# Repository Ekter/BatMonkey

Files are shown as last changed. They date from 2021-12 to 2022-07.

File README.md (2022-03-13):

# BatMonkey
This is the Bat Monkey, a monkey-like robot monitored by phone and controlled by arduino, whose purpose is to climb trees.

 [Gantt diagram]( https://online.officetimeline.com/shareable-link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)

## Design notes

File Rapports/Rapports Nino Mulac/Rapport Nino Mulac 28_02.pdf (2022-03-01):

# Bat Monkey

Rapport de la huitième séance(28 février) :
Pendant la séance, nous avons essayé le montage avec 8 moteurs. Nous ne l’avions jamais fait avant, et nous avons bien fait de vérifier que ça marche puisque la carte subit des pertes de tension le long de son circuit interne, qui empêchent plus de 4 moteurs d’être “attachés”(les moteurs se mettent ainsi à consommer du courant). Les 8 moteurs alimentés simultanément étaient parfois “ramollis” sans raison, et se laissaient tomber alors que le programme leur imposait un angle, ou se déplaçaient cran par cran quand on leur demandait un mouvement continu.
Nous avons désormais un “driver moteur” fait main par M. Masson équipé de câbles de cuivre de 1.5 mm qui conduisent beaucoup mieux l’électricité permettant ainsi d’éviter les chutes de tension.
Pendant la semaine, nous allons devoir tester les fonctions que nous avions écrites pour garder un mouvement linéaire par le calcul :
float getPhi(Servo servo, float i)
//i position de l'arbre par rapport au bras. ex: -1 indique 1 centimètre d'écart, 2 indique que le robot est enfoncé de 2 centimètres dans l'arbre
{
return acos(((i - 8.5 * cos(toAngle(servo.read()))) / 16));
}

float toAngle(float n)
{
return n * 3.14 / 180;
}

float toN(float a)
{
return a * 180 / 3.14;
}
Les fonctions toAngle et toN doivent être modifiées pour prendre en compte l’angle de chaque moteur, et tout devrait fonctionner ensuite.
Il ne nous restera qu’à découper les bras et y planter les clous.

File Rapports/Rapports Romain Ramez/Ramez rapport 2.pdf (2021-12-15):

## Ramez Romain

# BAT MONKEY SÉANCE N°2

J’ai commencé par finir la modalisation du Bat Monkey, en assemblant toutes les pièces entre elles, sur OneShape, et en modélisant un arbre pour mieux m’imager le principe de grimpe !

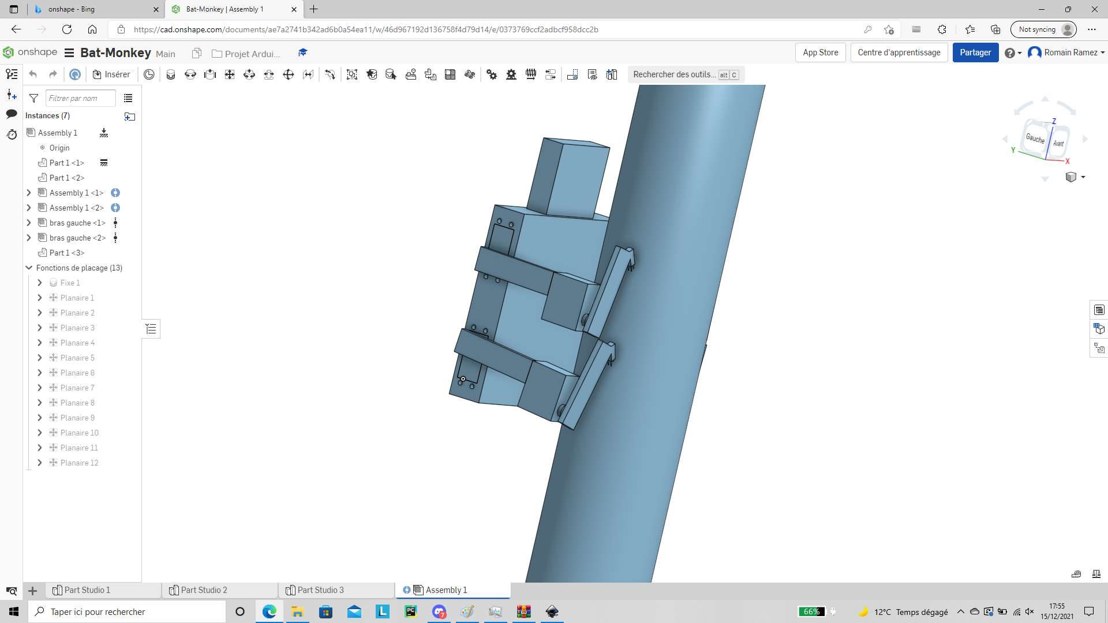
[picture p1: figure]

Ensuite, sous conseil du brillant professeur, nous avons décider de partir sur deux méthodes de grimpes différentes !
Je me suis donc mis à travailler sur une méthode où le Bat Monkey grimperai à l’arbre en s’accrochant (toujours à l’aide de piques) puis en se tractant à l’aide d’une crémaillère pour remonter au niveau des bras.

Modélisation du Bat Monkey

Modélisation des bras/ de la crémaillère
pour les premières tentative

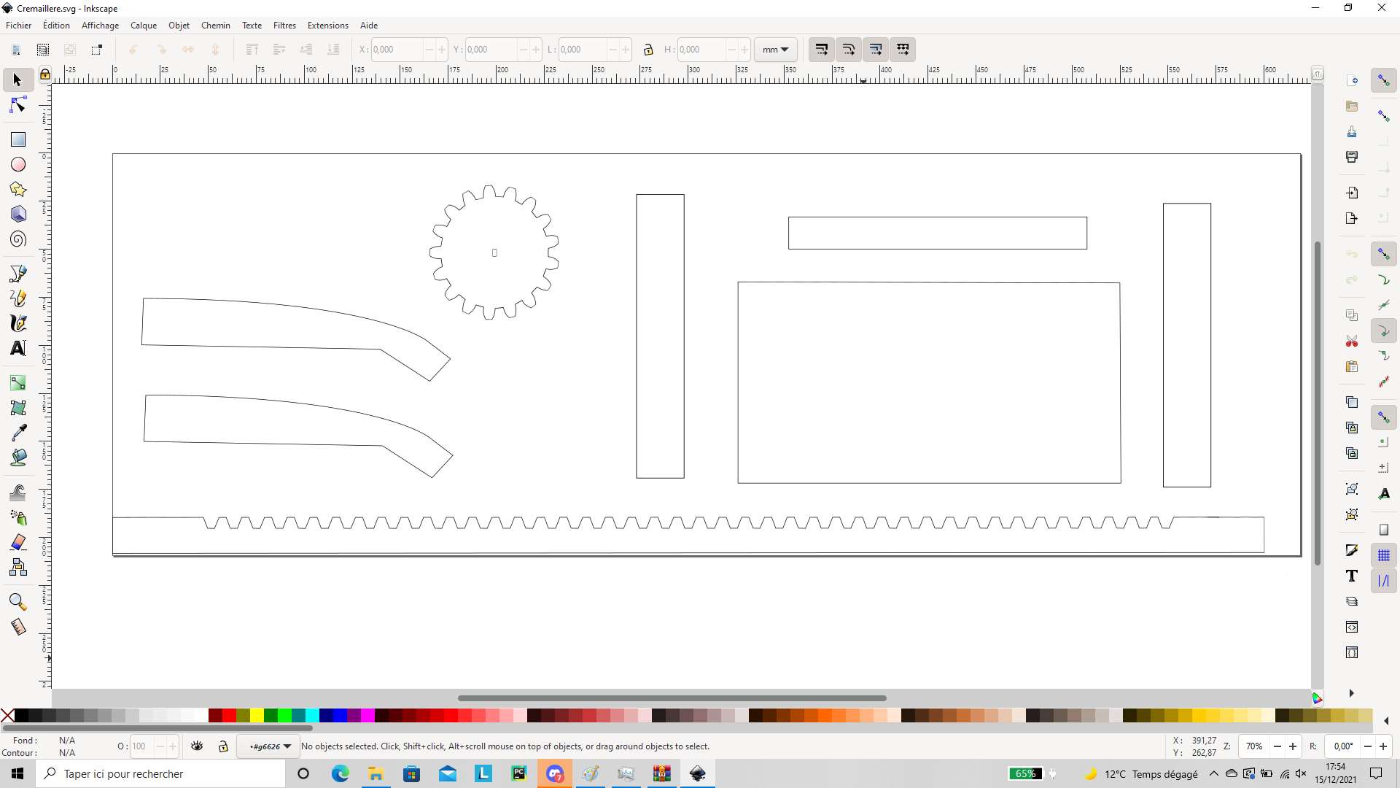
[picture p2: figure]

Enfin, j’ai pu aller faire découper tout cela à la coupeuse laser. Mais pour une raison que tout le monde ignore, le laser n’a pas transpercé le bois ( à 2 reprises… ), alors nous ne pouvons pas encore faire nos essais. Nous iront récupérer les morceaux de bois coupés vendredi au FabLab !

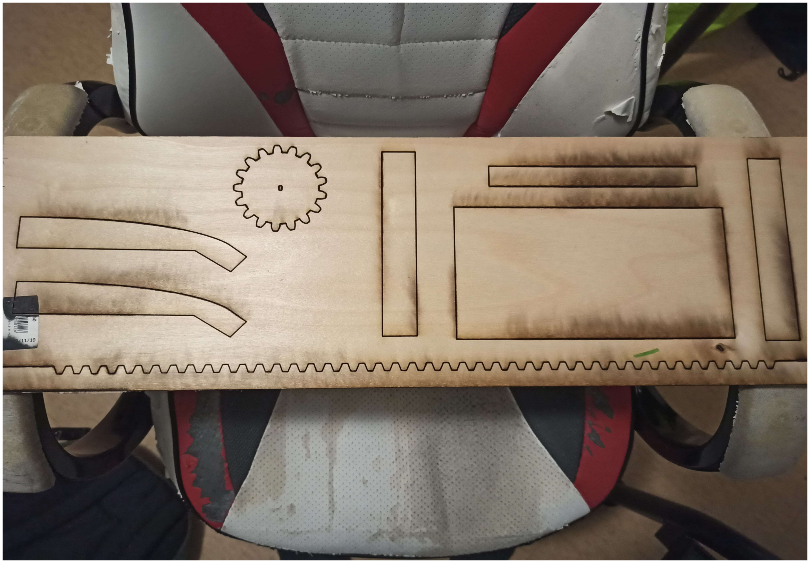
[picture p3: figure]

Planche de bois « presque » découpées

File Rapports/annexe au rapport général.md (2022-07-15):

# annexe

L'ensemble du programme est réécrit en algorithmes en language naturel [ici](https://github.com/Ekter/BatMonkey/tree/main/Code/algorithmes)

Vous pouvez aussi consulter le [code source](https://github.com/Ekter/BatMonkey/blob/main/Code/moteurs3/moteurs3.ino)

Ou voir la liste des composants et les shémas électroniques [ici](https://github.com/Ekter/BatMonkey/tree/main/Mod%C3%A8les/fritzing)

Au plaisir,

icon_BM

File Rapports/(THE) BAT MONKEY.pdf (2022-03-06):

# BAT MONKEY

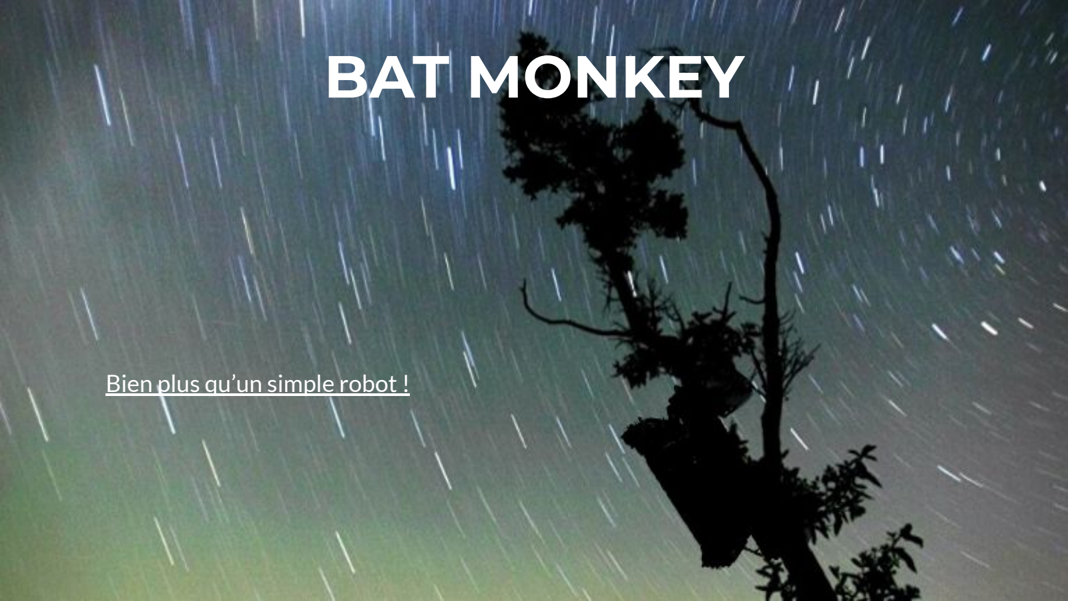
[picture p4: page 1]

### Bien plus qu’un simple robot !

# Sommaire

- L’idée
- Le plan
- Les échecs
- Les 1001 programmes
- Appli
- Son futur

# Pourquoi faire le Bat Monkey ?

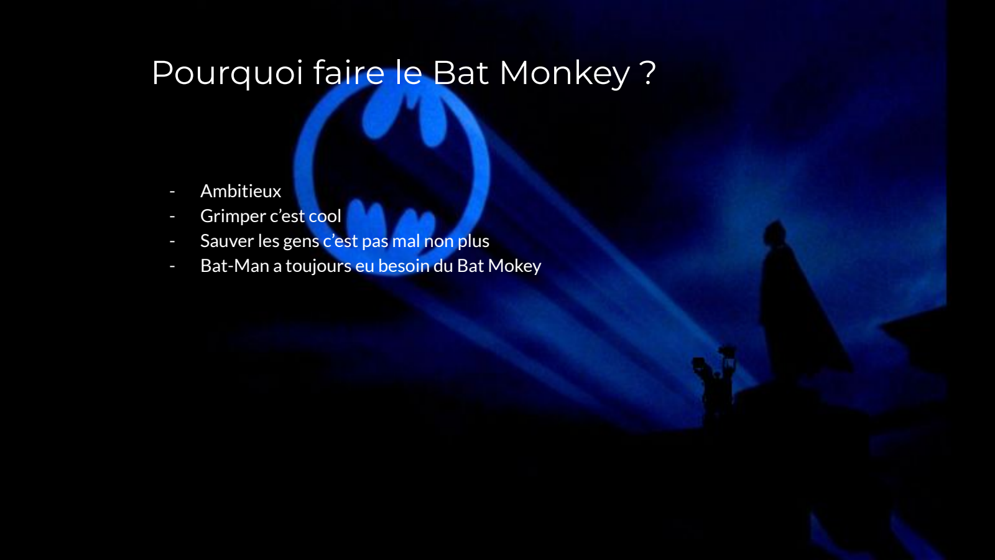
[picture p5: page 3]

- Ambitieux
- Grimper c’est cool
- Sauver les gens c’est pas mal non plus
- Bat-Man a toujours eu besoin du Bat Mokey

# Comment faire ?

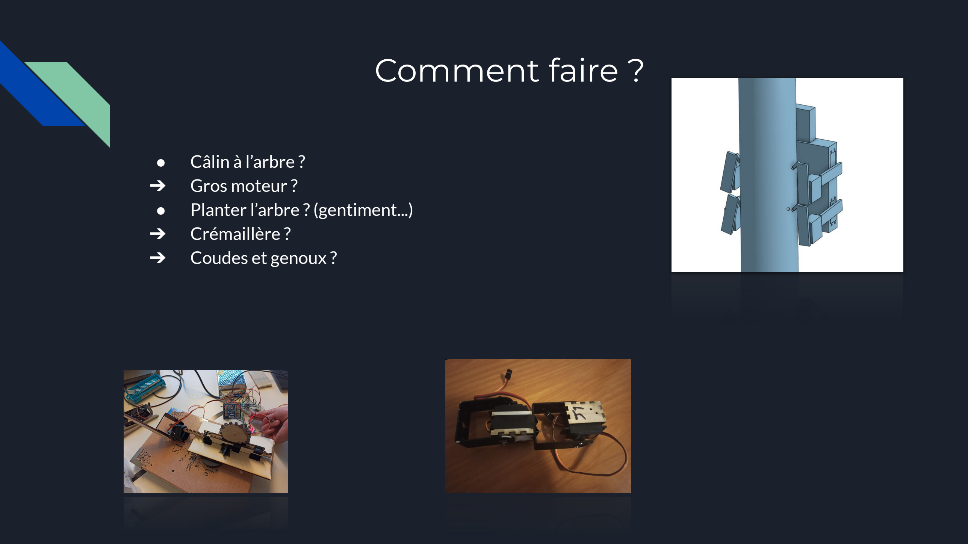
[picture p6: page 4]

- Câlin à l’arbre ?
➔ Gros moteur ?
- Planter l’arbre ? (gentiment...)
➔ | Crémaillère ?
➔ | Coudes et genoux ?

# Les ratés

# LA CREMAILLERE

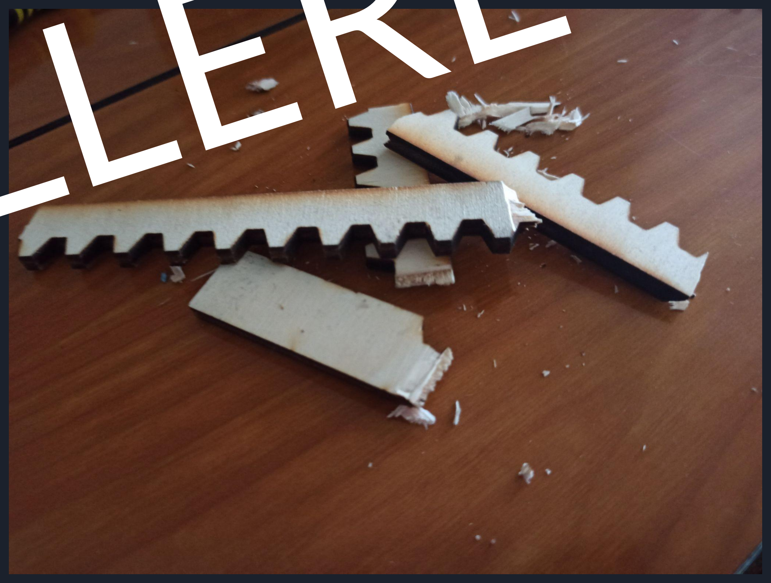
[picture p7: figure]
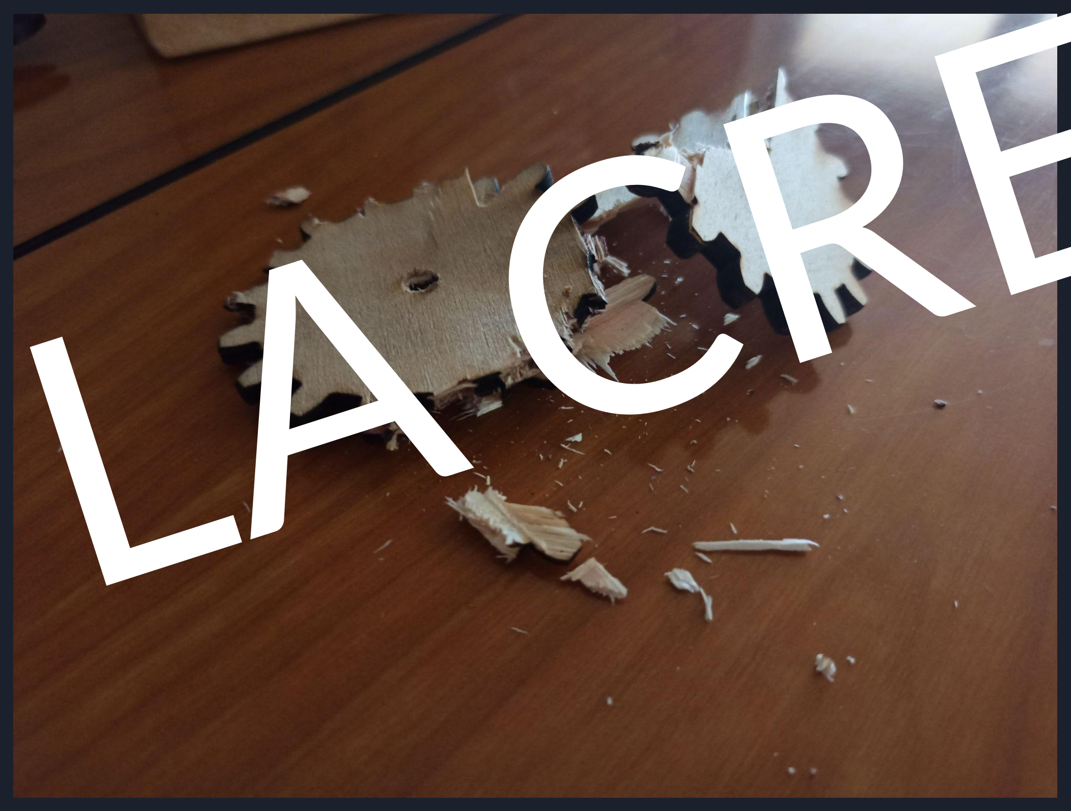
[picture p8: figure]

# La programmation

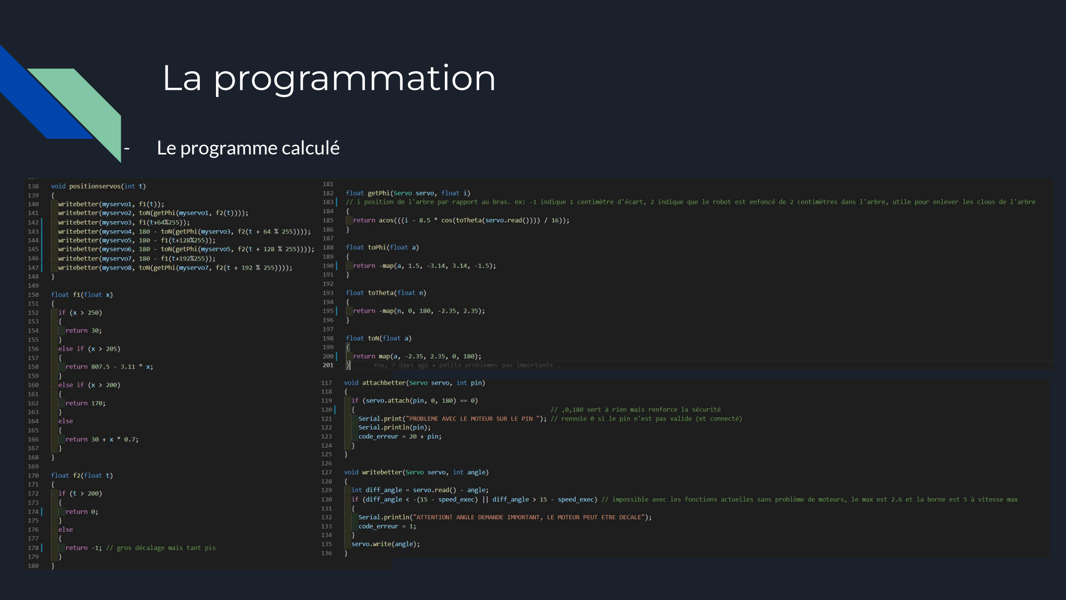
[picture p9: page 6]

- Le programme calculé

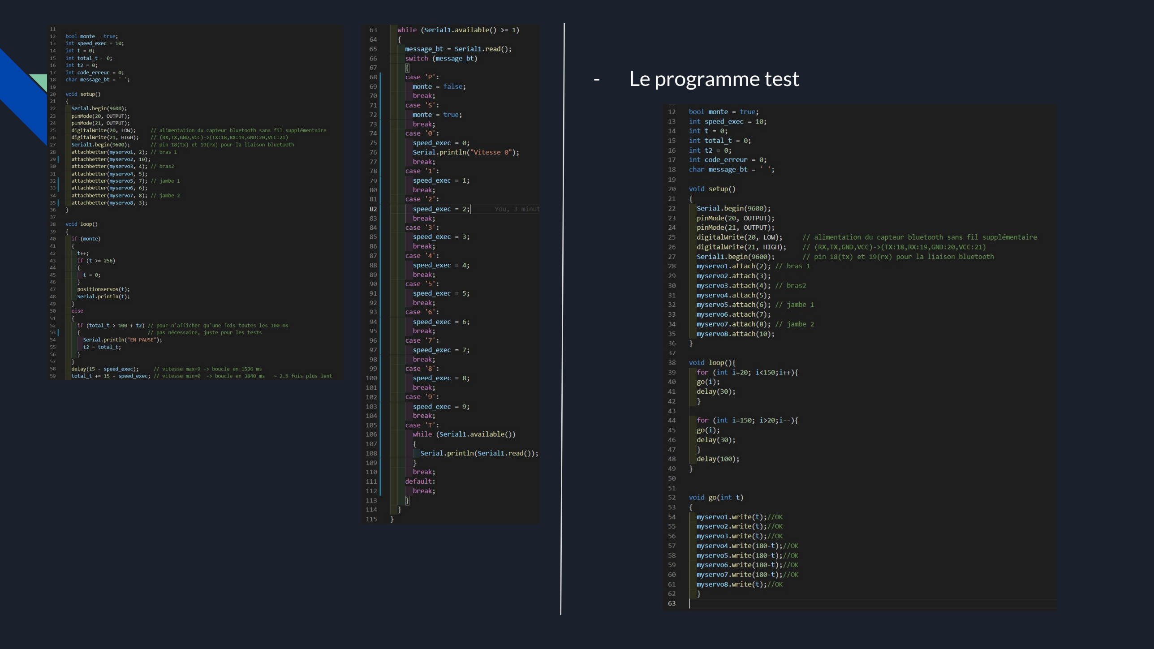
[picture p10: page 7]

- Le programme test

# L’appli

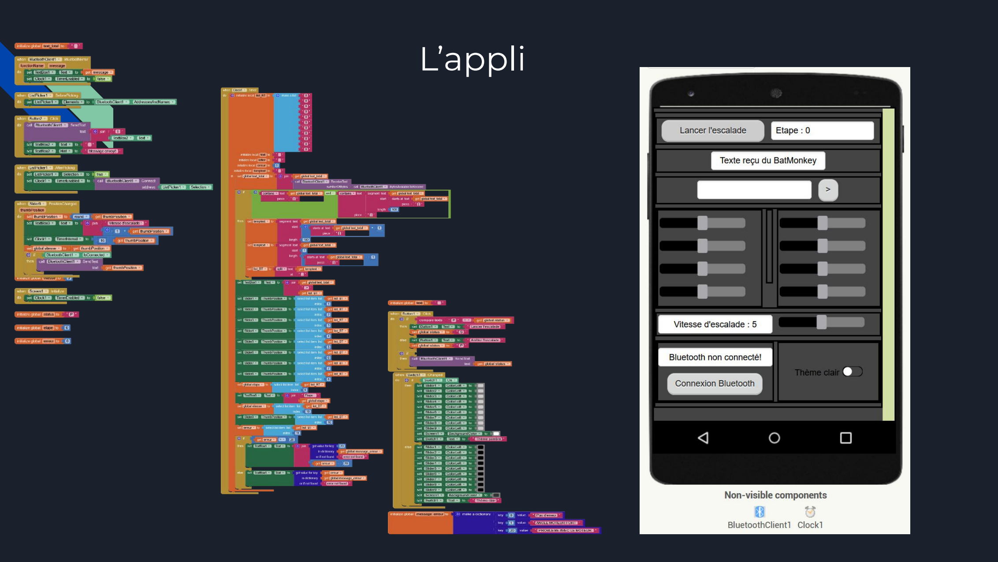
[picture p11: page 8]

# La suite…?

- De quoi mieux secourir
- Optimisation
- Lance rocket…
- En faire toute une armée

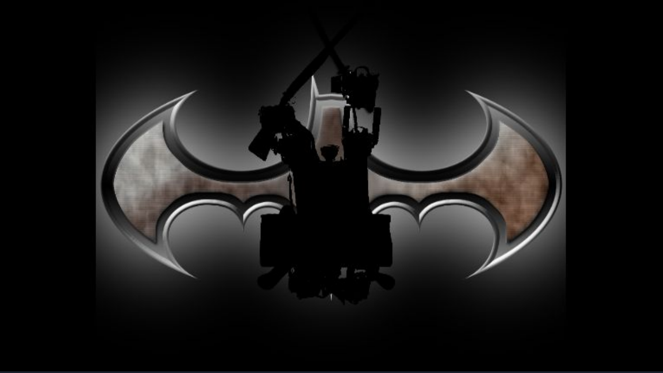
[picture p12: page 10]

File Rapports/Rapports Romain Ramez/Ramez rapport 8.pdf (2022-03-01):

# BAT MONKEY SÉANCE N°8

## Ramez Romain

Aujourd'hui nous n'avions qu'on seul but : faire ENFIN fonctionner les bras et jambes ensemble... Pour ce faire, nous avons commencé par passer à une alimentation de 55A, ce qui n'a pas résout le problème... C'est alors que M. Masson a trouvé une solution est nous à donc fabriqué un
« pseudo-driver moteur », ce qui devrait permettre aux moteurs de faire ce qu'on leur demande ! Nous avons également accrocher sa tête, car pour grimper aux arbres, il est important d 'avoir la tête sur les épaules !

## Cette séance :

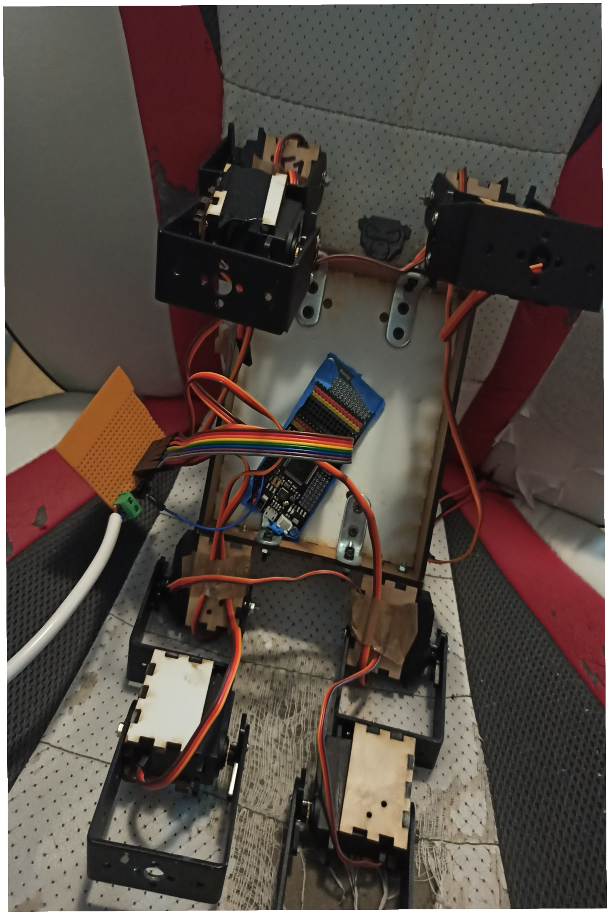
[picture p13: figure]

## Pour la prochaine séance :

Dans le but d'être le plus prêt possible lors de la présentation, nous allons (si le « pseudo-driver » fonctionne bien comme prévu) tester la finaliter de notre programme pour faire fonctionner le Bat Monkey et le corriger au besoin.
De plus, nous comptons également travailler sur le design du Bat Monkey afin qu'il est l'air plus « gentil » car nous ne perdons pas de vu son but qui est de sauver les gens !

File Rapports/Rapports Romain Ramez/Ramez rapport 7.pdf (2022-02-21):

## BAT MONKEY

## SÉANCE N°7

Ramez Romain

J’ai commencé cette 7ieme séance par changer de 90° les angles de chaque moteur afin de mieux régler leur champs de possibilité. Ensuite, j’ai monté la boite qui servira de corps au Bat Monkey, sur laquelle j’ai ensuite fixé chaque membres à leur place respective (c’est mieux ainsi…).

Le Bat Monkey enfin monté !

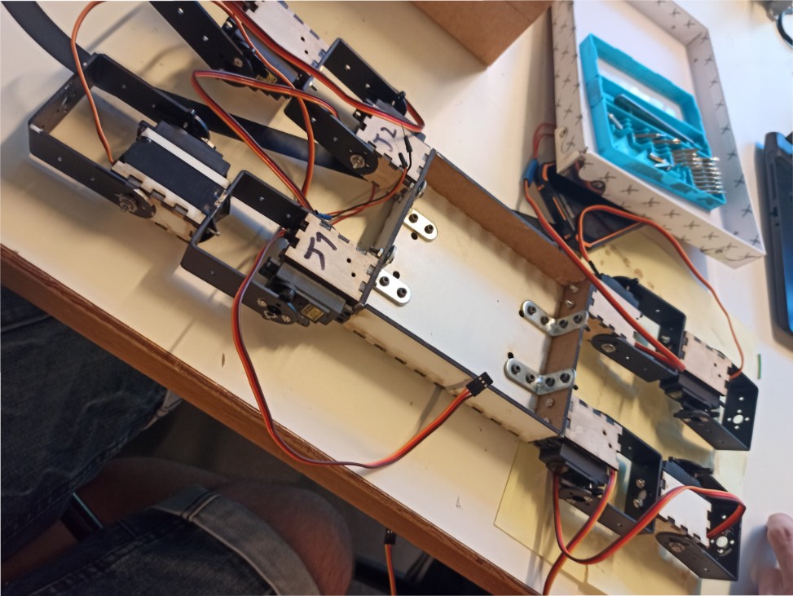
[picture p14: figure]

Ensuite nous avons fait les premiers « vrais » essaient pour voir si les mouvements qu’il faisait était ceux qu’il devait faire… Cela n’a pas été très concluant, mais ne nous nous attendions pas à ce que cela arrive du premier coup, c’est pourquoi nous avons prévu de faire plus de tentatives afin de présenter le meilleur projet de la JPO !

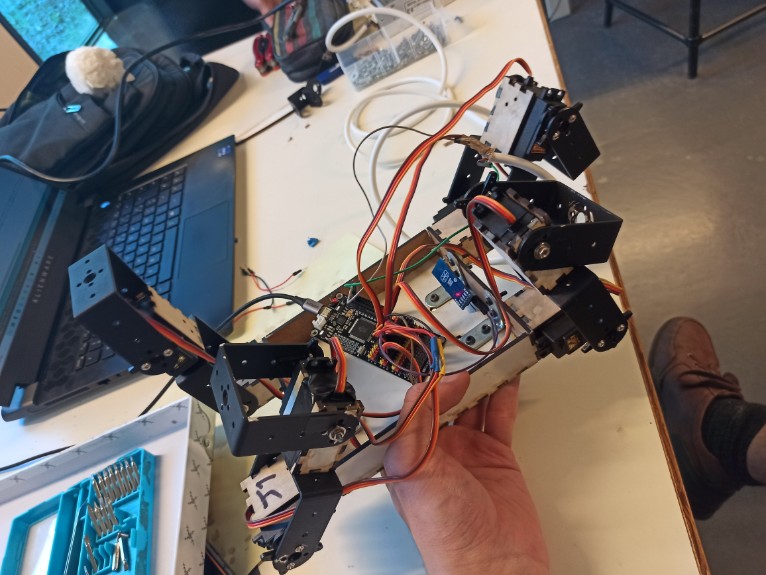
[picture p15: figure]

Les premiers mouvement !

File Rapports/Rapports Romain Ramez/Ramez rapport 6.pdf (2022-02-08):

## BAT MONKEY

### SEANCE N°6

Ramez Romain

Pendant cette séance, nous avons finis de monter les bras et les jambes que nous avions commencé hors cours quelques jours auparavant.

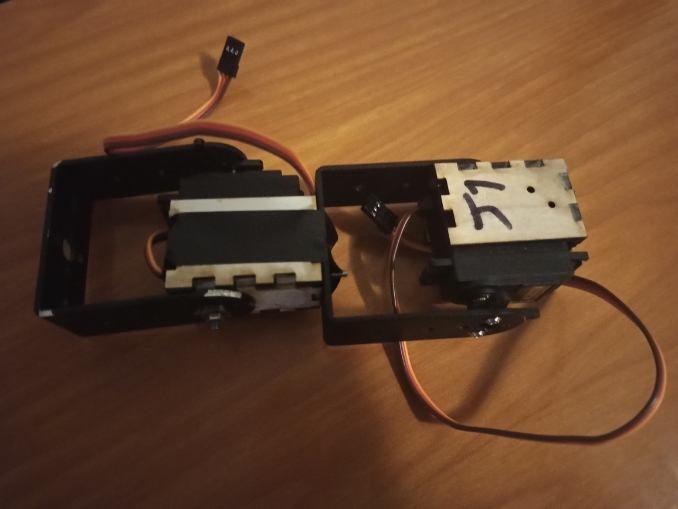
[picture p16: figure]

### Une des jambes

Et nous avons ensuite revu le code afin de donner le bon mouvement aux
membres ! Cette étape étant une des plus importantes et une des plus longues, elle nous aura duré tout le restant de la séance, et nous en sommes à 3/4..

### Exemple de code

### Lien vers la vidéo d’un des membres en mouvement void monterJ2() {

delay(250);
myservo7.write(100); // Vers arrière
delay(250);
myservo8.write(100) ;// Vers arrière delay(250);
myservo7.write(0);
}

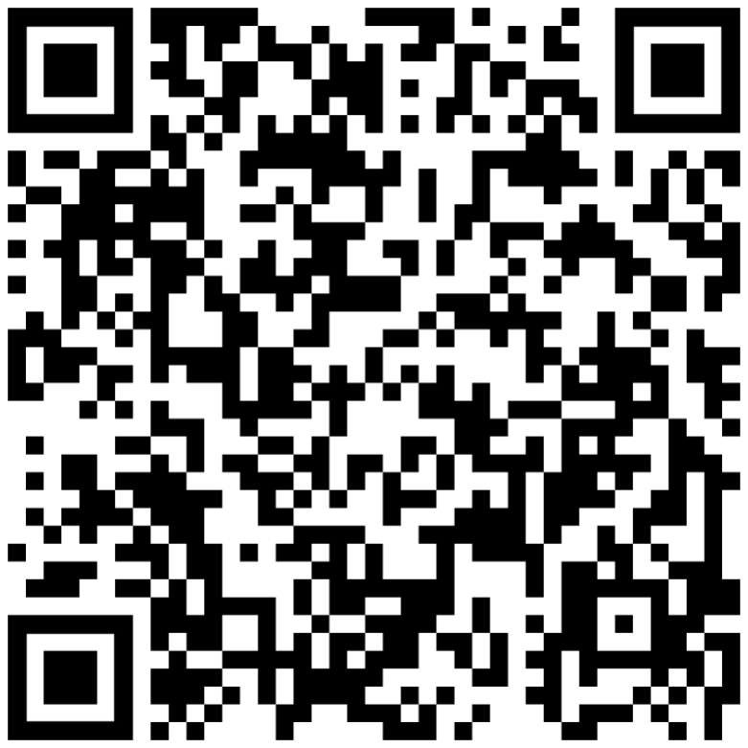
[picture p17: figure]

void baisserJ2(int t) {
myservo7.write(180 - t / 1.4); myservo8.write(minj2 - t);
}

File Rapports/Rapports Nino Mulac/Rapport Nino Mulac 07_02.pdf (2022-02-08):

# Bat Monkey

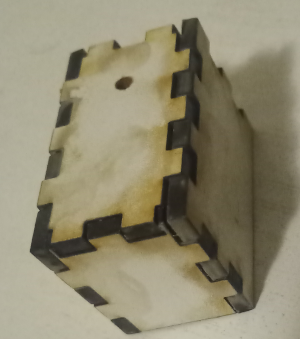
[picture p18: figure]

Rapport de la sixième séance(7 février) :
Pendant la semaine, nous avons monté les membres du robot avec les boites découpées au laser. Il nous manquait quand même un moteur, donc nous n’avons pu finir que durant la séance. Voilà ce que donne la jambe droite une fois montée :

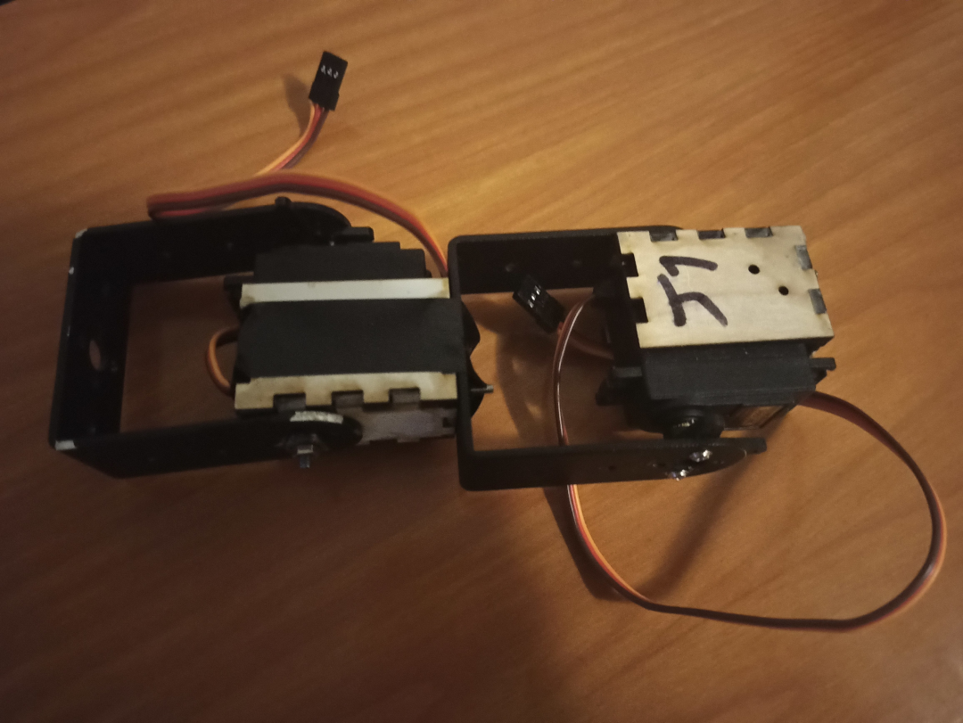
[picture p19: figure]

Nous n’avons pas fermé les boites, pour pouvoir sortir les moteurs en cas de problème. Ensuite, nous avons modifié le programme que Romain avait fait pendant la dernière séance pour l’adapter aux angles des différents servomoteurs, comme
chaque moteur est un modèle différent. Voilà ce que donnait le
programme pour une jambe fonctionnelle (le bout de la jambe
toujours aligné sur sa base) en le passant sur l’autre bras :

Les deux jambes sont bonnes, un des deux bras est partiellement fini et l’autre n’est pas encore fait.

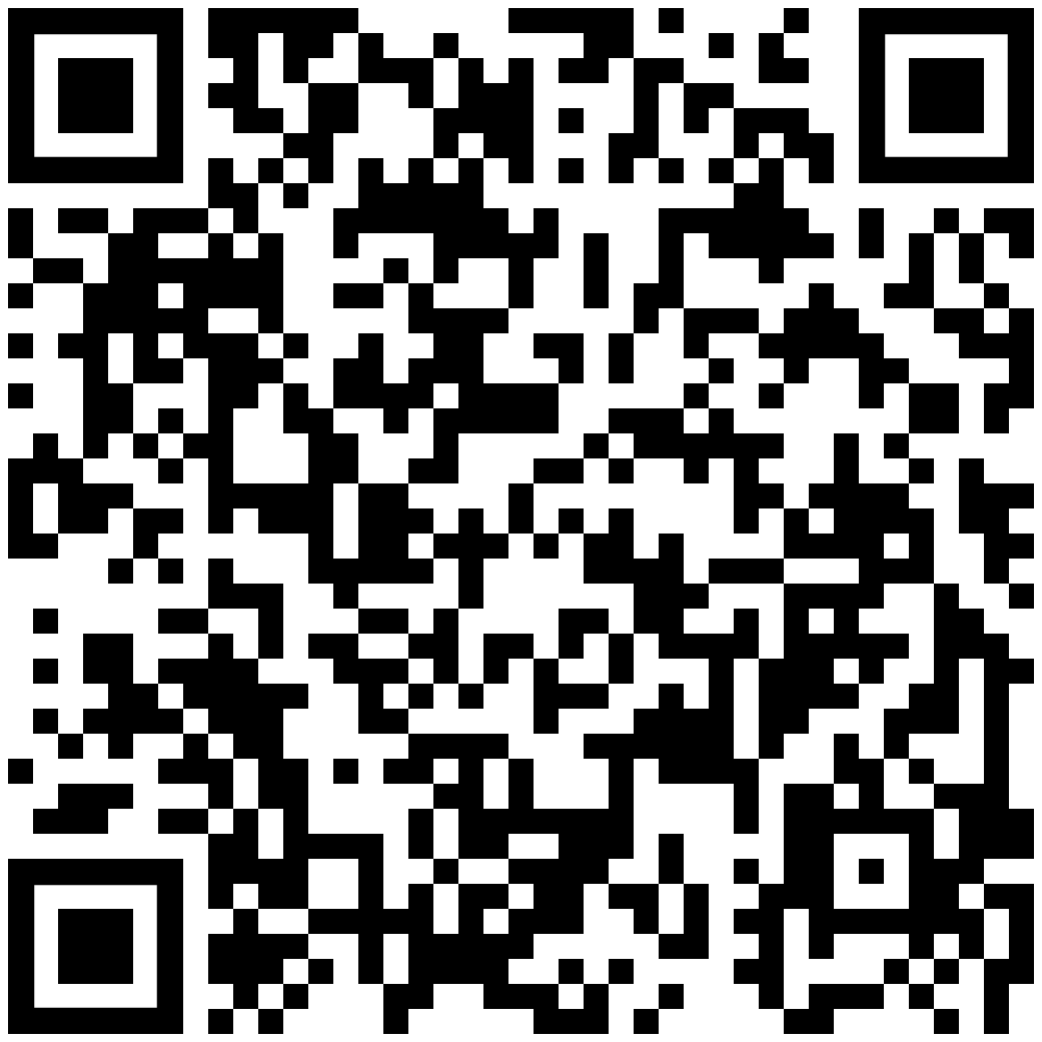
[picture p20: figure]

Il est pas mignon notre serpent ?

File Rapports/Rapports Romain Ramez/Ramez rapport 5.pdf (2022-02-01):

# BAT MONKEY SÉANCE N°

# Ramez Romain

# Au début de cette nouvelle séance, je me suis occupé du code principal du Bat

Monkey, c’est à dire des actions principales telles que monter les bras, les jambes..

# Cela de façon coordonnée afin de pouvoir grimper au mieux !

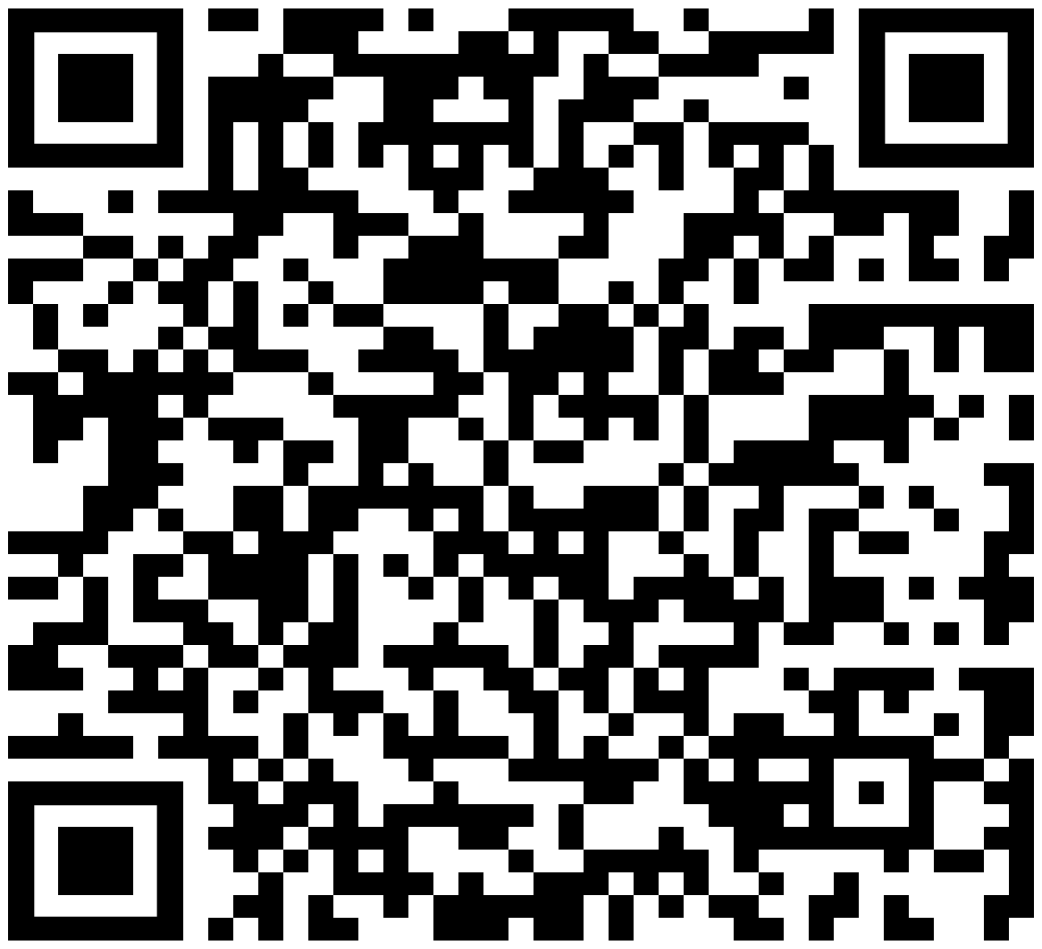
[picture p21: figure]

# Une fois cela fini, et ne pouvant pas encore commencer les nombreux tests, j’ai commencé à coller les morceaux de bois découpés par mon camarade afin de faire

des « boites » pour tenir les moteurs.

void loop() {
while (monte) {
e1();
affichestat();
e2();
affichestat();
e3();
affichestat();
e4();
affichestat();
}
}

void e1() { // Peut-être i=4 et i-- ?! monterb1();
baisserb2();
baisserJ1();
baisserJ2();
i++;
}

void e2() {
monterJ1();
baisserb2();
baisserb1();
baisserJ2();
i++;

void monterb1() {
myservo.write(MAXORMIN); // Vers arrière myservo2.write(MAXORMIN); // Vers arrière myservo.write(MINORMAX);
}

void baisserb1() {
myservo.write(i * 50 + 64); // le 50 est arbitraire !
myservo2.write(180 - i * 40 * 1.4); // le 50 est arbitraire !
}

## Voici une partie de ce code

## Et une vidéo de ce qu'il renvoie (les positions des membres!) :

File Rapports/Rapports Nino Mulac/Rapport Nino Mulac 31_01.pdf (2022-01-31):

# Bat Monkey

Rapport de la cinquième séance(31 janvier) :
Aujourd’hui, Romain et moi avons fabriqué des boites en bois pour y mettre les moteurs comme les pièces en aluminium coûtent trop cher. Voici le patron que nous avons utilisé :

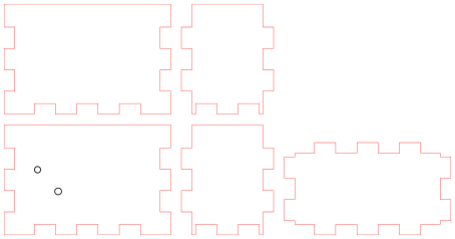
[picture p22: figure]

Les trous en gris serviront à mettre des vis. Voilà le rendu final :

Ici, le trou sur le dessus a été rajouté à la perceuse.


Et voilà une vidéo du programme qu’a fait Romain pour le contrôle des moteurs des bras et des jambes en asynchrone, on peut y voir les angles de chaque moteur à tout instant (ces orientations sont encore libres de changer).

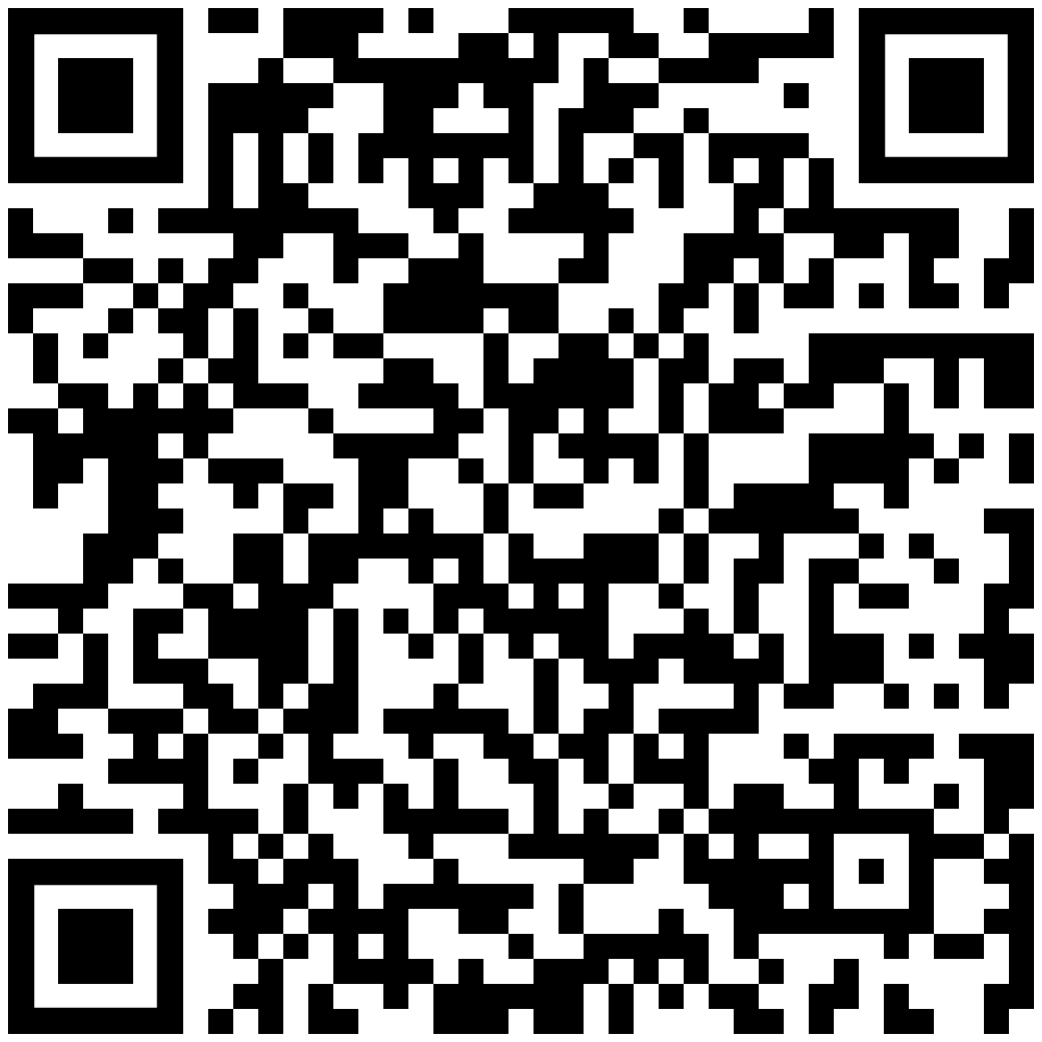
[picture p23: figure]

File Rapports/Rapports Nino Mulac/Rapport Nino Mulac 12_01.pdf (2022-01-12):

# Bat Monkey

Rapport de la quatrième séance(5 janvier) :
Aujourd’hui, Romain et moi avons monté une jambe du robot avec le bras que nous avions déjà (par manque de pièces), puis, une fois que les professeurs sont passés pour noter notre prestation à l’oral, nous avons pu démonter son bras-crémaillère pour récupérer les pièces nécessaires à la fabrication d’un nouveau bras. Nous avons aussi beaucoup réfléchi à la façon dont le robot devait escalader, et avons choisi que le robot devrait lever un membre, puis se soulever sur les trois autres d’un quart de l’amplitude maximale, et replanter le membre soulevé le plus haut possible. Ainsi le robot pourra avoir une escalade “linéaire” et montera petit bout par petit bout, plutôt que de monter le corps indépendamment des membres. Mais le corps devra coller le plus possible à l’arbre pour éviter que
le centre de gravité ne s’éloigne trop, donc nous avons dû trouver des fonctions
par lesquelles modifier les angles extrêmes pour que la course du clou par
rapport au corps soit linéaire. Comme vous pouvez le voir, c’est difficile :

Voici les fonctions que nous avons gardées finalement : myservo3.write(val + 20);
myservo4.write(180 - val * 1.5);
myservo.write(val + 64);
myservo2.write(180 - val * 1.4);

Avec val l’angle que nous donnions sur le potentiomètre divisé par 5, les servo 1 et 2 assignés au bras, et les 3 et 4 aux jambes.

Voilà deux vidéos de démonstration de fonctionnement, de 4 et 5 secondes, les membres sont contrôlés par le potentiomètre :

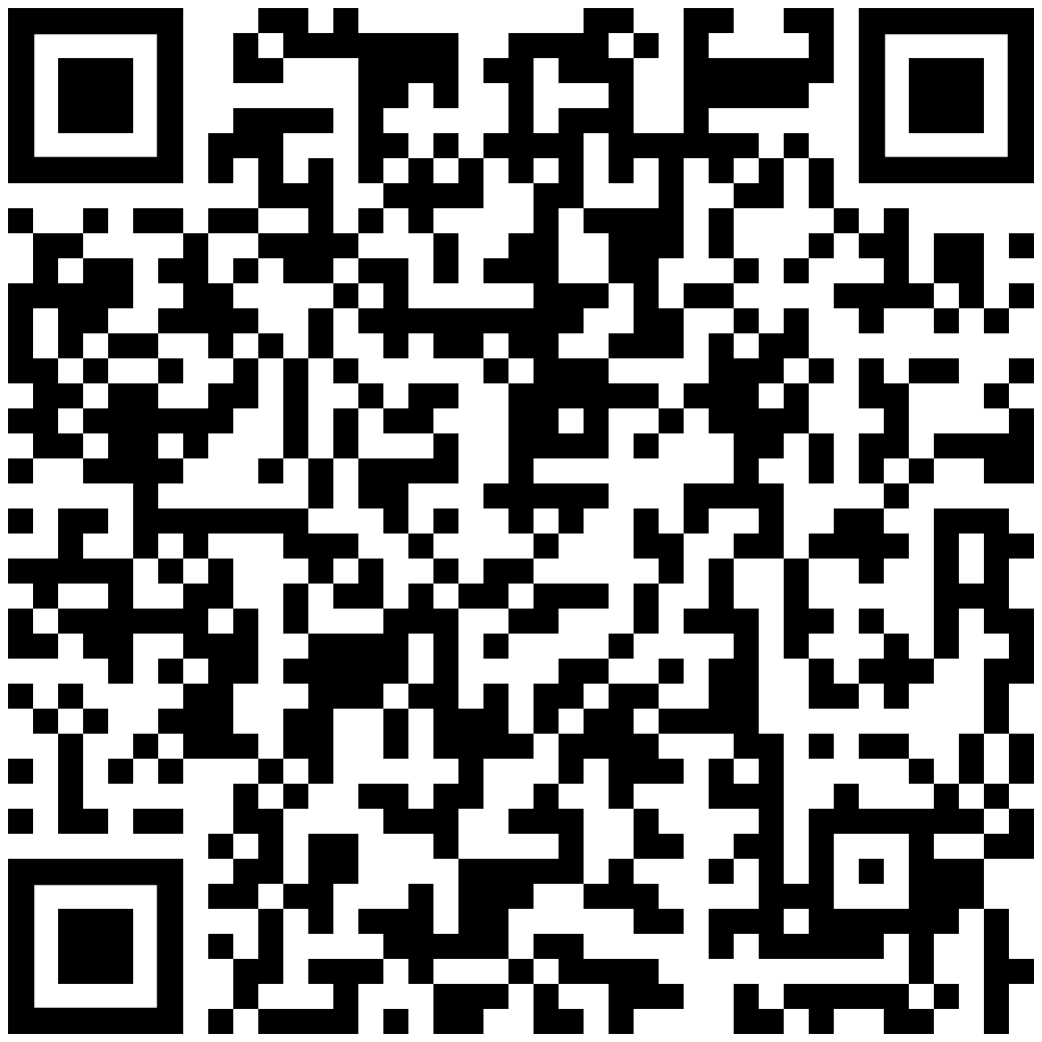
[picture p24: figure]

Pour continuer, il nous faudra imprimer ou commander de nouvelles pièces pour les bras. En effet, nous avons épuisé les stocks…

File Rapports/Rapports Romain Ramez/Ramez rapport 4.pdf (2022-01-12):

# BAT MONKEY

### SÉANCE N°4

### Ramez Romain

Ayant avorté l’idée de la crémaillère, j’ai rejoins l’idée de mon camarade qui est de faire des bras et des jambes avec des coudes afin d’imiter notre manière de monter aux arbres (plus ou moins...).
J’ai alors commencé par mettre sur papier nos idées de comment faire cela au niveau de la programmation et de la technique.


Ensuite, nous avons monté la première jambe et écris le programme pour que celleci puisse simuler une grimpe : comme si nous plantions notre pied et que nous poussions ensuite sur notre jambes pour se hisser. Une fois les branchement fait, nous avions notre première jambes !
Nous avons ensuite fait un bras, avec le même but.

Fonctionnement
du Bat Monkey

Un bras et une jambe !
(vidéo :
https://cdn.discordapp.com/attachments/754633399406428240/930789309609558066/VID_20220112_124255.mp4 (https://cdn.discordapp.com/attachments/754633399406428240/930789309609558066/VID_20220112_124255.mp4)
)


Pour la suite, nous allons donc devoir commander/imprimer de nouvelles pièces… Ainsi nous auront tout nos bras et jambes, et nous pourrons commencer les essais !!

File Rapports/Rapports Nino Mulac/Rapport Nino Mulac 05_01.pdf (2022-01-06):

# Bat Monkey

Rapport de la troisième séance(5 janvier) :

Aujourd’hui j’ai fait le montage électronique pour contrôler deux servomoteurs. Le principal obstacle étant le manque de puissance électrique fournie par la carte(elle suffit pour alimenter un moteur, mais pas plus, et nous pourrions avoir besoin de jusqu’à 8 servomoteurs), nous devons donc désormais utiliser une alimentation externe plus puissante, mais aussi plus contraignante. En effet, il sera difficile de grimper aux arbres avec une rallonge…


Le Bat Monkey est aussi dorénavant équipé de clous au bout de ses bras qui lui serviront à s’accrocher dans le bois, mais il faut faire attention à ses mouvements incontrôlés qui arrivent trop souvent lors des tests, et qui manquèrent de peu de piquer Romain qui travaillait sur sa crémaillère.
Mon bras fonctionnant alors correctement, j’ai aidé Romain à terminer le sien. En effet, il avait un problème de couple avec son moteur pas à pas, qui n’arrivait qu’à grand-peine à faire tourner son engrenage, et encore moins à pousser la barre crantée qui lui permettrait de monter.

Voici des liens vers des vidéos de fonctionnement du bras(2s et 6s respectivement) :


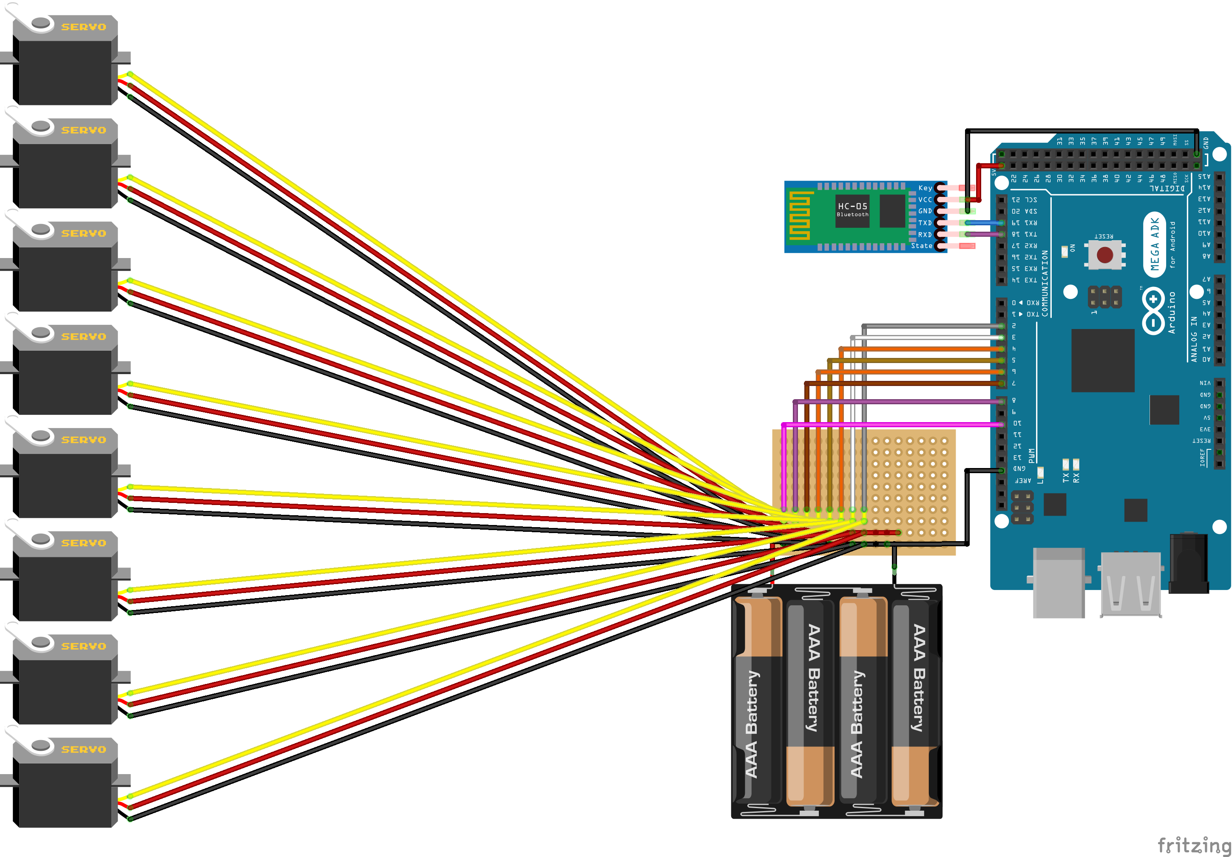
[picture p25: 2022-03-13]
Modèles/fritzing/BATMONKEYYRYY_bb.png

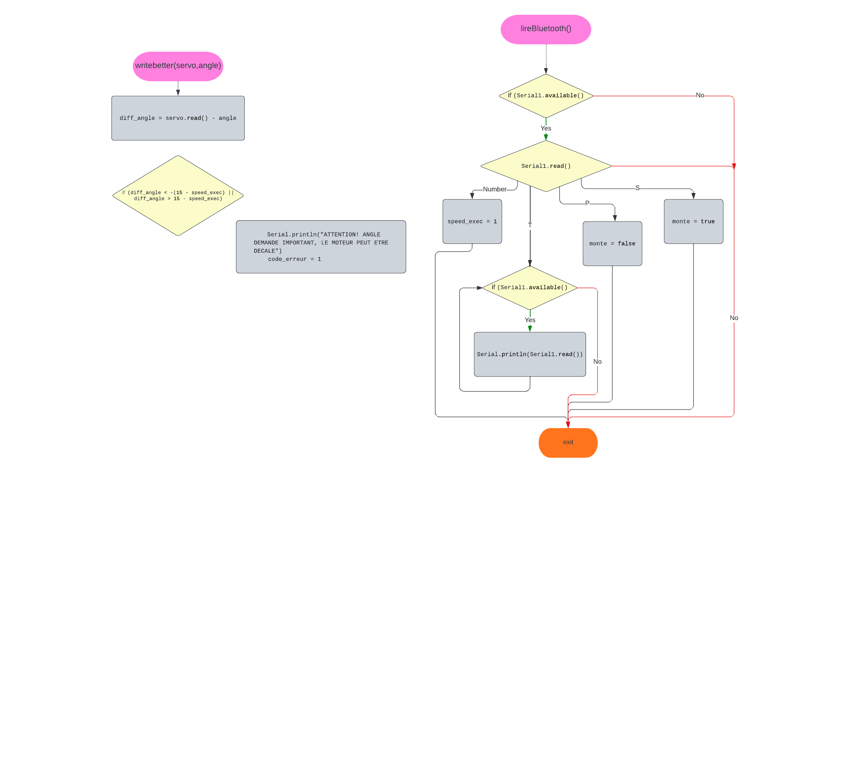
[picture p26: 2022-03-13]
Code/algorithmes/loop_-_Page_2.png

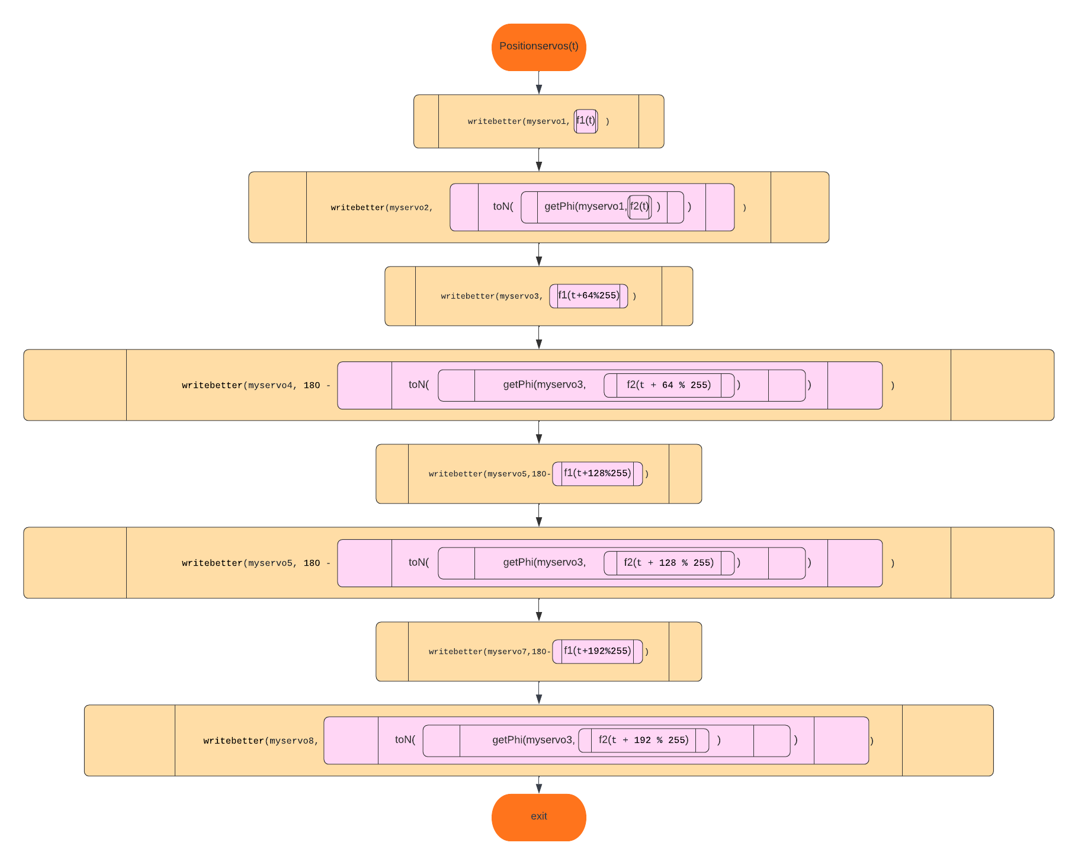
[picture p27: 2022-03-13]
Code/algorithmes/positionservos.png

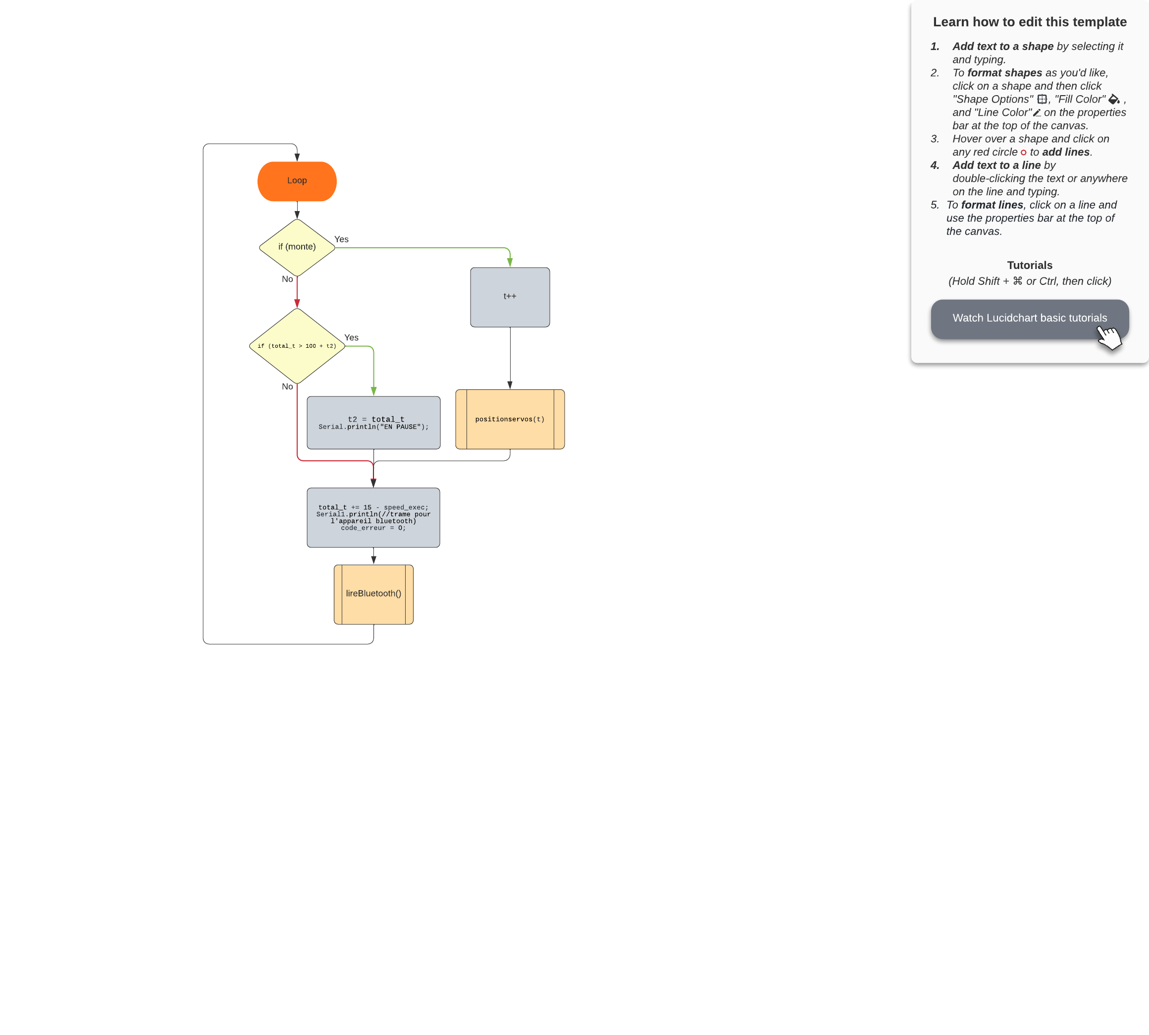
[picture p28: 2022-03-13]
Code/algorithmes/loop_-_Loop.png

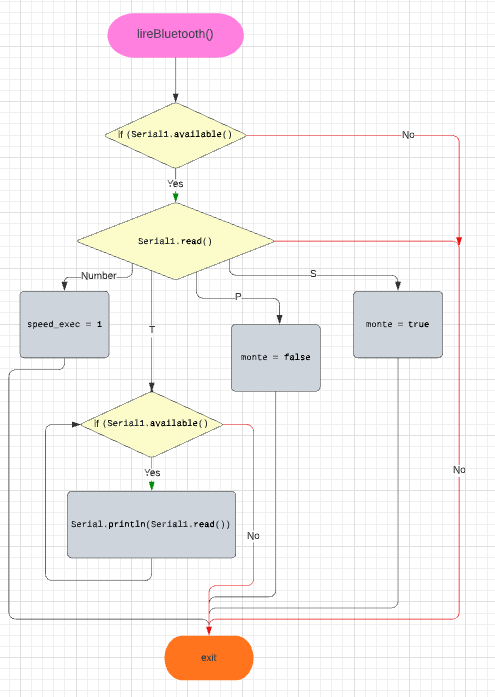
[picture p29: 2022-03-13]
Code/algorithmes/lireBluetooth.png

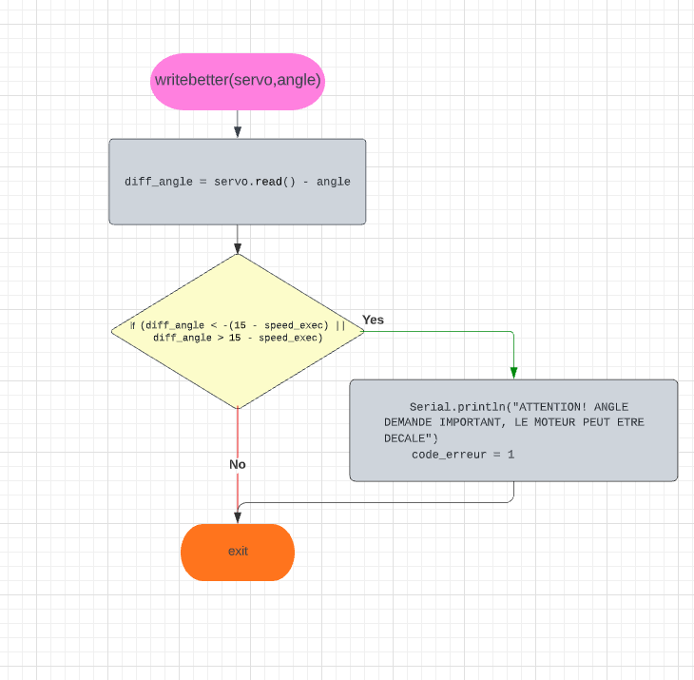
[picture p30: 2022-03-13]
Code/algorithmes/writebetter.png

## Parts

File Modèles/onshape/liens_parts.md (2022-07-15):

# pièces 3d

Corps bat monkey:
    [Pièce](https://cad.onshape.com/documents/c982648adeff445b06480f78/w/532ba9cda7de4ce549d25be7/e/d16ef1af9c4f6687c0e493e5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 "lien onshape")

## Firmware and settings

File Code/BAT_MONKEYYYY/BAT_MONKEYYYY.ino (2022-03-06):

#include <Servo.h>

Servo myservo1;
Servo myservo2;
Servo myservo3;
Servo myservo4;
Servo myservo5;
Servo myservo6;
Servo myservo7;
Servo myservo8;

bool monte = true;
int speed_exec = 10;
int t = 0;
int total_t = 0;
int code_erreur = 0;
char message_bt = ' ';
int i = 0;
int t1 = 20;
int t2 = 52;
int t3 = 84;
int t4 = 126;
int tp1 = 1;
int tp2 = 1;
int tp3 = 1;
int tp4 = 1;

void setup()
{
  Serial.begin(9600);
  pinMode(20, OUTPUT);
  pinMode(21, OUTPUT);
  digitalWrite(20, LOW);  // alimentation du capteur bluetooth sans fil supplémentaire
  digitalWrite(21, HIGH); // (RX,TX,GND,VCC)->(TX:18,RX:19,GND:20,VCC:21)
  Serial1.begin(9600);    // pin 18(tx) et 19(rx) pour la liaison bluetooth
  myservo1.attach(2);     // bras 1
  myservo2.attach(3);
  myservo3.attach(4); // bras2
  myservo4.attach(5);
  myservo5.attach(6); // jambe 1
  myservo6.attach(7);
  myservo7.attach(8); // jambe 2
  myservo8.attach(10);
}

void loop()
{
  go1(t1);      //J1 complete
  go2(t2);     //J2 complete
  go3(t3); // B2 complet
  go4(t4); //  B1 complet
  if (t1 >= 150)
  {
    tp1 = -4;
  }
  if (t2 >= 150)
  {
    tp2 = -4;
  }
  if (t3 >= 150)
  {
    tp3 = -4;
  }
  if (t4 == 150)
  {
    tp4 = -4;
  }
  if (t1 <= 20)
  {
    tp1 = 1;
  }
  if (t2 <= 20)
  {
    tp2 = 1;
  }
  if (t3 <= 20)
  {
    tp3 = 1;
  }
  if (t4 <= 20)
  {
    tp4 = 1;
  }
  t1 += tp1;
  t2 += tp2;
  t3 += tp3;
  t4 += tp4;
  delay(15 - speed_exec);
  Serial1.println("[" + String(myservo1.read()) + "," + String(myservo2.read()) + "," + String(myservo3.read()) + "," + String(myservo4.read()) + "," + String(myservo5.read()) + "," + String(myservo6.read()) + "," + String(myservo7.read()) + "," + String(myservo8.read()) + "," + String(t1) + "," + String(speed_exec) + "," + String(code_erreur) + "]");
  Serial.println("[" + String(myservo1.read()) + "," + String(myservo2.read()) + "," + String(myservo3.read()) + "," + String(myservo4.read()) + "," + String(myservo5.read()) + "," + String(myservo6.read()) + "," + String(myservo7.read()) + "," + String(myservo8.read()) + "," + String(t1) + "," + String(speed_exec) + "," + String(code_erreur) + "]");
  code_erreur = 0;
  while (Serial1.available() >= 1)
  {
    message_bt = Serial1.read();
    switch (message_bt)
    {
    case 'P':
      monte = false;
      break;
    case 'S':
      monte = true;
      break;
    case '0':
      speed_exec = 0;
      Serial.println("Vitesse 0");
      break;
    case '1':
      speed_exec = 1;
      break;
    case '2':
      speed_exec = 2;
      break;
    case '3':
      speed_exec = 3;
      break;
    case '4':
      speed_exec = 4;
      break;
    case '5':
      speed_exec = 5;
      break;
    case '6':
      speed_exec = 6;
      break;
    case '7':
      speed_exec = 7;
      break;
    case '8':
      speed_exec = 8;
      break;
    case '9':
      speed_exec = 9;
      break;
    case 'T':
      while (Serial1.available())
      {
        Serial.println(Serial1.read()); // completement inutile
      }
      break;
    default:
      break;
    }
  }
}

void go1(int t)
{  myservo3.write(t);

  myservo2.write(t);
}
void go2(int t)
{  myservo7.write(180 - t);

  myservo4.write(180 - t);
}
void go3(int t)
{
  myservo5.write(180 - t);
  myservo6.write(180 - t);
}
void go4(int t)
{
  myservo1.write(t);

  myservo8.write(t);
}

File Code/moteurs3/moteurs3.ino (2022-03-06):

#include <Servo.h>

Servo myservo1;
Servo myservo2;
Servo myservo3;
Servo myservo4;
Servo myservo5;
Servo myservo6;
Servo myservo7;
Servo myservo8;

bool monte = true;
int speed_exec = 10;
int t = 0;
int total_t = 0;
int t2 = 0;
int code_erreur = 0;
char message_bt = ' ';

void setup()
{
  Serial.begin(9600);
  pinMode(20, OUTPUT);
  pinMode(21, OUTPUT);
  digitalWrite(20, LOW);     // alimentation du capteur bluetooth sans fil supplémentaire
  digitalWrite(21, HIGH);    // (RX,TX,GND,VCC)->(TX:18,RX:19,GND:20,VCC:21)
  Serial1.begin(9600);       // pin 18(tx) et 19(rx) pour la liaison bluetooth
  attachbetter(myservo1, 2); // bras 1
  attachbetter(myservo2, 10);
  attachbetter(myservo3, 4); // bras2
  attachbetter(myservo4, 5);
  attachbetter(myservo5, 7); // jambe 1
  attachbetter(myservo6, 6);
  attachbetter(myservo7, 8); // jambe 2
  attachbetter(myservo8, 3);
}

void loop()
{
  if (monte)
  {
    t++;
    if (t >= 256)
    {
      t = 0;
    }
    positionservos(t);
    Serial.println(t);
  }
  else
  {
    if (total_t > 100 + t2) // pour n'afficher qu'une fois toutes les 100 ms
    {                       // pas nécessaire, juste pour les tests
      Serial.println("EN PAUSE");
      t2 = total_t;
    }
  }
  total_t += 15 - speed_exec; // vitesse min=0  -> boucle en 3840 ms   ~ 2.5 fois plus lent
  Serial1.println("[" + String(myservo1.read()) + "," + String(myservo2.read()) + "," + String(myservo3.read()) + "," + String(myservo4.read()) + "," + String(myservo5.read()) + "," + String(myservo6.read()) + "," + String(myservo7.read()) + "," + String(myservo8.read()) + "," + String(t) + "," + String(speed_exec) + "," + String(code_erreur) + "]");
  Serial.println("[" + String(myservo1.read()) + "," + String(myservo2.read()) + "," + String(myservo3.read()) + "," + String(myservo4.read()) + "," + String(myservo5.read()) + "," + String(myservo6.read()) + "," + String(myservo7.read()) + "," + String(myservo8.read()) + "," + String(t) + "," + String(speed_exec) + "," + String(code_erreur) + "]");
  code_erreur = 0;
  while (Serial1.available() >= 1)
  {
    message_bt = Serial1.read();
    switch (message_bt)
    {
    case 'P':
      monte = false;
      break;
    case 'S':
      monte = true;
      break;
    case '0':
      speed_exec = 0;
      Serial.println("Vitesse 0");
      break;
    case '1':
      speed_exec = 1;
      break;
    case '2':
      speed_exec = 2;
      break;
    case '3':
      speed_exec = 3;
      break;
    case '4':
      speed_exec = 4;
      break;
    case '5':
      speed_exec = 5;
      break;
    case '6':
      speed_exec = 6;
      break;
    case '7':
      speed_exec = 7;
      break;
    case '8':
      speed_exec = 8;
      break;
    case '9':
      speed_exec = 9;
      break;
    case 'T':
      while (Serial1.available())
      {
        Serial.println(Serial1.read()); // completement inutile
      }
      break;
    default:
      break;
    }
  }
}

void attachbetter(Servo servo, int pin)
{
  if (servo.attach(pin, 0, 180) == 0)
  {                                                      // ,0,180 sert à rien mais renforce la sécurité
    Serial.print("PROBLEME AVEC LE MOTEUR SUR LE PIN "); // renvoie 0 si le pin n'est pas valide (et connecté)
    Serial.println(pin);
    code_erreur = 20 + pin;
  }
}

void writebetter(Servo servo, int angle)
{
  int diff_angle = servo.read() - angle;
  if (diff_angle < -(15 - speed_exec) || diff_angle > 15 - speed_exec) // impossible avec les fonctions actuelles sans problème de moteurs, le max est 2.6 et la borne est 5 à vitesse max
  {
    Serial.println("ATTENTION! ANGLE DEMANDE IMPORTANT, LE MOTEUR PEUT ETRE DECALE");
    code_erreur = 1;
  }
  servo.write(angle);
}

void positionservos(int t)
{
  writebetter(myservo1, f1(t));
  writebetter(myservo2, toN(getPhi(myservo1, f2(t))));
  writebetter(myservo3, f1(t+64%255));
  writebetter(myservo4, 180 - toN(getPhi(myservo3, f2(t + 64 % 255))));
  writebetter(myservo5, 180 - f1(t+128%255));
  writebetter(myservo6, 180 - toN(getPhi(myservo5, f2(t + 128 % 255))));
  writebetter(myservo7, 180 - f1(t+192%255));
  writebetter(myservo8, toN(getPhi(myservo7, f2(t + 192 % 255))));
}

float f1(float x)
{
  if (x > 250)
  {
    return 30;
  }
  else if (x > 205)
  {
    return 807.5 - 3.11 * x;
  }
  else if (x > 200)
  {
    return 170;
  }
  else
  {
    return 30 + x * 0.7;
  }
}

float f2(float t)
{
  if (t > 200)
  {
    return 0;
  }
  else
  {
    return -1; // gros décalage mais tant pis
  }
}

float getPhi(Servo servo, float i)
// i position de l'arbre par rapport au bras. ex: -1 indique 1 centimètre d'écart, 2 indique que le robot est enfoncé de 2 centimètres dans l'arbre, utile pour enlever les clous de l'arbre
{
  return acos(((i - 8.5 * cos(toTheta(servo.read()))) / 16));
}

float toPhi(float a)
{
  return -map(a, 1.5, -3.14, 3.14, -1.5);
}

float toTheta(float n)
{
  return -map(n, 0, 180, -2.35, 2.35);
}

float toN(float a)
{
  return map(a, -2.35, 2.35, 0, 180);
}

// float ftout(t){
//   return map(t,0,255,1,180);
// }

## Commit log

2021-11-20 ajout du cahier des charges
2021-12-05 liens cliquables pour le fichier Rapports Nino Mulac(passe de .txt à .md)
2022-01-12 ajout rapports sénce 4 + code bras+jambe
    [BAT_MONKEYYYY.ino]
2022-01-31 ajout rapport 31/01, manque encore celui de romain
2022-02-08 ajout rapport séance 07/02, manque celui de romain
2022-02-14 code qui marche avec les fonctions pour les angles des moteurs+modélisation
2022-02-14 suppression de commentaires
2022-02-17 la sécurisation du code avance
2022-02-18 ajout de l'icone de l'application
2022-02-19 corrections diverses sur l'application
    [Bat_monkey_moteurs2.ino]
2022-03-04 nouvelles fonctions pour gérer les angles au lieu des positions
2022-03-12 Ajout modélisation Fritzing
    [BATMONKEYYRYY.fzz]
2022-07-15 HAHAHAHAHA le bat monkey reprend de l'activité bientôt on le verra sauter sur des gens pour les égorger...
